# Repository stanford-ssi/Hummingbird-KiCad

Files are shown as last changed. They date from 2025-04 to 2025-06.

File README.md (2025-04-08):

# Hummingbird-KiCad

## Latest Updates

Apr 7, 2025 (Koichi K.): Created the PCB layout. Next steps: figure out power and traces.

Apr 6, 2025 (Sam C.): modified the schematic to be ready for layout. Linked all of the necessary footprints for parts. Added mfr, supplier, cost info. Action item: verification and layout.

Feb 23, 2025 (Victor H., Sam C., Jesse F., Luis S. and Pete!): Modified the KiCad schematic to include correct numbers of PTs, TTs, LCs, etc. (based on P&ID V4). Schematics are organized hierarchically. Problem: Still need to check for input/output conflicts. Action item: can add custom connector footprints next time.

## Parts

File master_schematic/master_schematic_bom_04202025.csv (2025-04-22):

Reference | Value | Datasheet | Footprint | Qty | Manufacturer | Manufacturer Part # | Supplier | Supplier Part # | Unit Cost | Cost @ Qty | Manufacturer 2 | Manufacturer Part # 2 | Supplier 2 | Supplier Part # 2 | Unit Cost 2 | Cost @ Qty 2
U1 | RFM95 | https://learn.adafruit.com/adafruit-rfm69hcw-and-rfm96-rfm95-rfm98-lora-packet-padio-breakouts/overview | hb_footprint_lib:rfm95_connector | 1 | Sullins Connector Solutions | PPPC091LFBN-RC | Digikey | PPPC091LFBN-RC | 0.63 | 0.63 | Sullins Connector Solutions | PPPC051LFBN-RC | Digikey | PPPC051LFBN-RC | 0.43 | 0.43
U9,U10,U11 | HX711 | https://learn.adafruit.com/adafruit-hx711-24-bit-adc | hb_footprint_lib:hx711_connector | 3 | Sullins Connector Solutions | PPPC061LFBN-RC | Digikey | PPPC061LFBN-RC | 0.47 | 0.47
U4,U5,U6,U7,U8 | MCP9600_Module | https://learn.adafruit.com/adafruit-mcp9600-i2c-thermocouple-amplifier/overview | hb_footprint_lib:mcp9600_connector | 5 | Sullins Connector Solutions | PPPC091LFBN-RC | Digikey | PPPC091LFBN-RC | 0.63 | 0.63
SW1 | SW_SPST | Datasheet | hb_footprint_lib:SW_1201M2S3AQE2 | 1 | C&K | 1201M2S3AQE2 | Digikey | CKN5054-ND | 14.68000 | 14.68000
R2,R3,R6,R8,R10,R12,R14,R15,R17 | 2.7K | https://industrial.panasonic.com/cdbs/www-data/pdf/RDM0000/AOA0000C307.pdf | Resistor_SMD:R_0805_2012Metric_Pad1.20x1.40mm_HandSolder | 9 | Panasonic Electronic Components | ERJ-6GEYJ272V | Digikey | P2.7KACT-ND | 0.10 | 0.042
R1,R4,R5,R7,R9,R11,R13,R16,R18 | 1K | https://industrial.panasonic.com/cdbs/www-data/pdf/RDM0000/AOA0000C307.pdf | Resistor_SMD:R_0805_2012Metric_Pad1.20x1.40mm_HandSolder | 9 | Panasonic Electronic Components | ERA-6AEB102V | Digikey | P1.0KDACT-ND | 0.10 | 0.066
Q1,Q2,Q3,Q4,Q5,Q6,Q7,Q8,Q9,Q10 | CWDM3011N TR13 PBFREE | https://my.centralsemi.com/datasheets/CWDM3011N.PDF | Package_SO:SOIC-8_3.9x4.9mm_P1.27mm | 10 | Central Semiconductor Corp | CWDM3011N TR13 PBFREE | Digikey | 1514-CWDM3011NTR13PBFREECT-ND | 1.09 | 1.09
J64,J65,J66,J67,J68,J69,J70,J71,J72,J73,J74,J75,J76,J77,J78,J79,J80,J81,J82,J83 | 1722563102 | https://www.literature.molex.com/SQLImages/kelmscott/Molex/PDF_Images/987651-1008.PDF |  | 20 | Molex | 1722563102 | Digikey | WM26332-ND | 0.30 | 0.25
J34,J35,J36,J37,J38,J39,J40,J41,J42,J43,J44,J45,J46,J47,J48,J49,J50,J51,J52,J53 | 0430250400 | https://tools.molex.com/pdm_docs/ps/PS-43045.pdf |  | 20 | Molex | 0430250400 | Digikey | WM1784-ND | 0.39 | 0.334
J23 | 12V Male | https://www.tme.com/Document/580f3494beb0741fbf705c7febbc9402/XT60H-F.pdf |  | 1 | Changzhou Amass Elec | XT60-F | LCSC | C98734 | 0.3547 | 0.3547
J22 | 5V Male | https://www.mouser.com/datasheet/2/564/JST_B4B_PH_SM4_TB_LF_SN_ePH-3481264.pdf |  | 1 | JST Commercial | PHR-2 | Mouser | 306-PHR-2PP | 0.10 | 0.10
J21 | 5V Female | https://www.mouser.com/datasheet/2/564/JST_B4B_PH_SM4_TB_LF_SN_ePH-3481264.pdf | hb_footprint_lib:JST_S2B-PH-SM4-TB | 1 | JST Commercial | S2B-PH-SM4-TB(LF)(SN) | Mouser | 306-S2BPHSM4TBLFSN | 0.51 | 0.51
J11,J12,J13,J14,J15,J16,J17,J18,J19,J20,J54,J55,J56,J57,J58,J59,J60,J61,J62,J63 | 1723103102 | https://www.molex.com/en-us/products/part-detail/1723103102?display=pdf | hb_footprint_lib:CONN02_1723103102_MOL | 20 | Molex | 1723103102 | Digikey | 900-1723103102-ND | 0.85 | 0.725
J2,J3,J4,J5,J6,J7,J8,J9,J10,J24,J25,J26,J27,J28,J29,J30,J31,J32,J33 | 0430450400 | https://tools.molex.com/pdm_docs/ps/PS-43045.pdf | -- ミックスされた値 -- | 19 | Molex | 0430450400 | Digikey | WM1814-ND | 1.42 | 1.207
J1 | 12V Female | https://www.lcsc.com/datasheet/lcsc_datasheet_2401181031_Changzhou-Amass-Elec-XT60PW-M_C98732.pdf | hb_footprint_lib:AMASS_XT60PW-M | 1 | Changzhou Amass Elec | XT60PW-M | LCSC | C98732 | 0.59 | 0.59
D1,D2,D3,D4,D5,D6,D7,D8,D9,D10 | SBRT20U60SP5-7 | https://www.diodes.com/assets/Datasheets/SBRT20U60SP5.pdf | hb_footprint_lib:POWERDI5_DIO | 10 | Diodes Incorporated | SBRT20U60SP5-7 | Digikey | SBRT20U60SP5-7DICT-ND | 0.78 | 0.78
C1,C2,C3,C4,C5,C6,C7,C8,C9,C10 | 0.1u | https://datasheets.kyocera-avx.com/KGM_X7R.pdf | Capacitor_SMD:C_0805_2012Metric | 10 | KYOCERA AVX | KGM21NR71H104KT | Digikey | 478-KGM21NR71H104KTCT-ND | 0.08 | 0.026

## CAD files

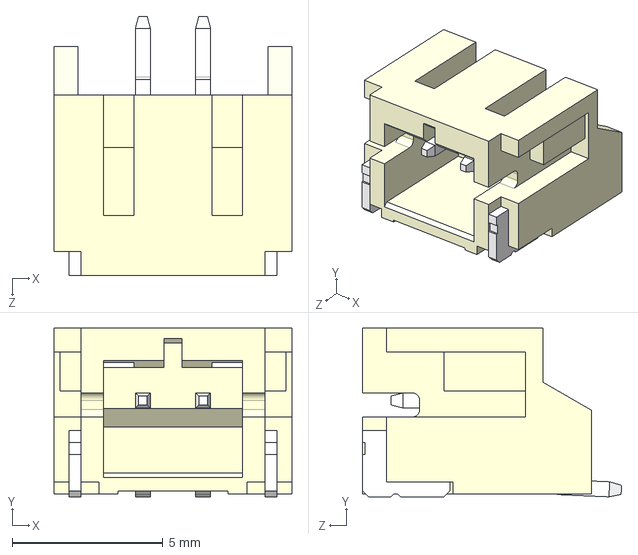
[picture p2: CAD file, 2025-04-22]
3dmodels/S2B-PH-SM4-TB.STEP
7.90 x 5.60 x 8.60 mm

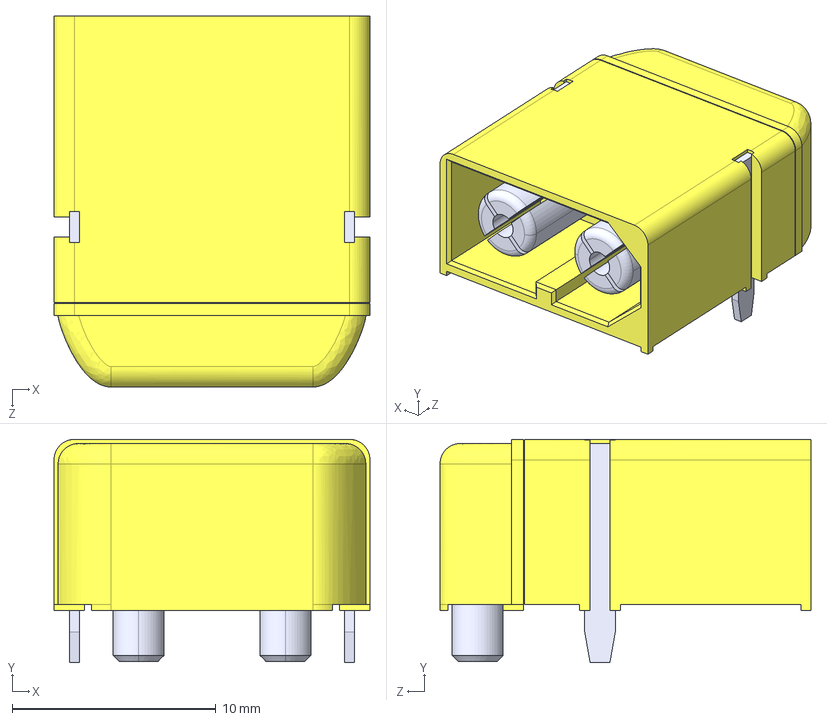
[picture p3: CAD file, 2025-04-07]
3dmodels/XT60PW-M.step
15.5 x 11.0 x 18.2 mm

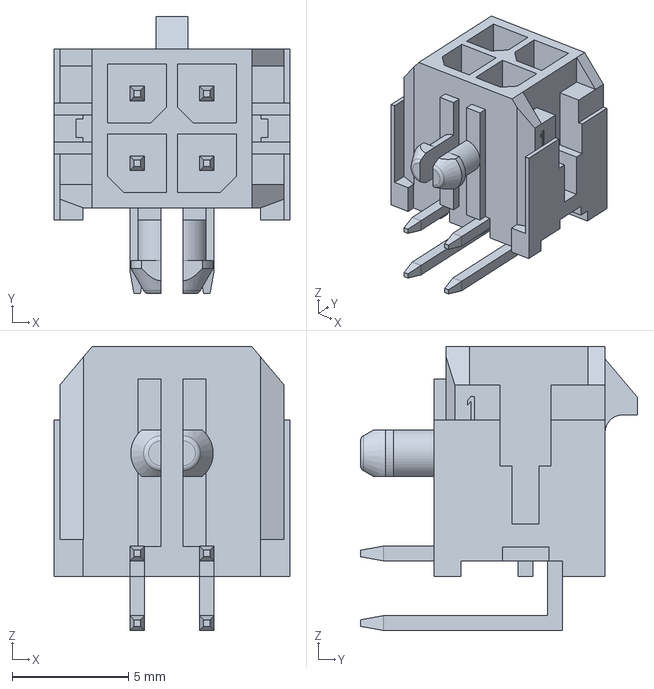
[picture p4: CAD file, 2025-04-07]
3dmodels/430450400.stp
10.2 x 11.9 x 12.2 mm

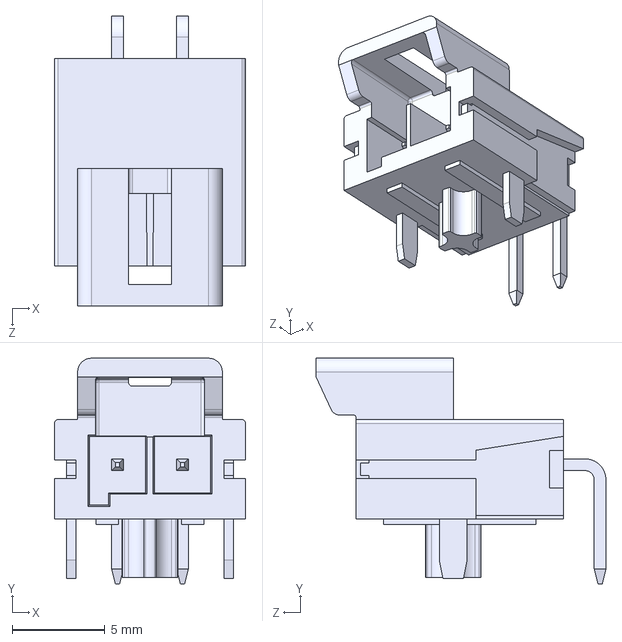
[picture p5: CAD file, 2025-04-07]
3dmodels/1723103102.step
10.3 x 12.2 x 15.6 mm

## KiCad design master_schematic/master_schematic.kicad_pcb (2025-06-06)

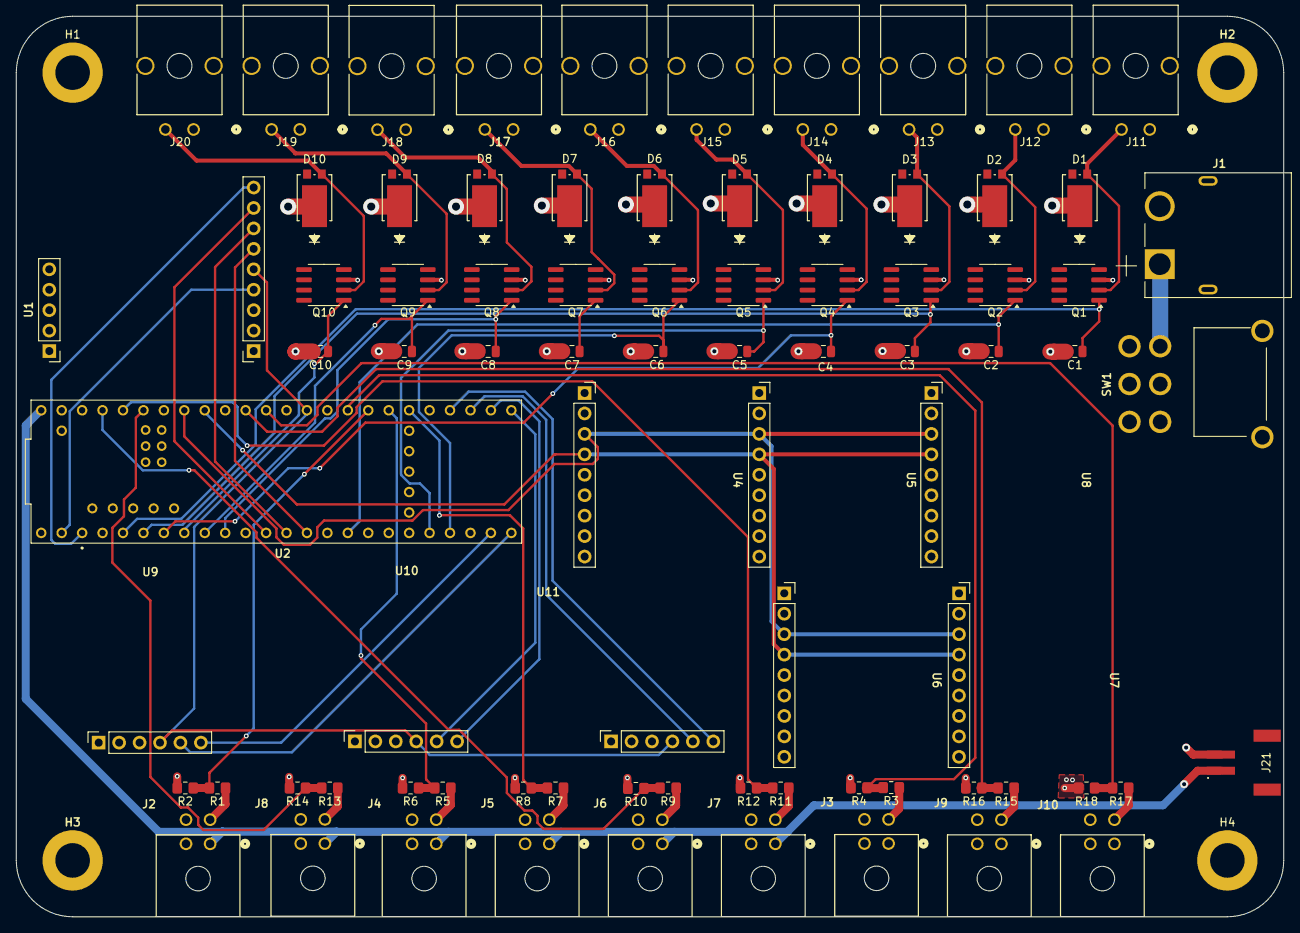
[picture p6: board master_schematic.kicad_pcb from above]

Board: 4 copper layers, 157.5 x 111.9 mm, 85 parts (0 on the bottom side), 57 nets.

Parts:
C1, C2, C3, C4, C5, C6, C7, C8, C9, C10: 0.1u; C_0805_2012Metric
D1, D2, D3, D4, D5, D6, D7, D8, D9, D10: SBRT20U60SP5-7; POWERDI5_DIO
H1, H2, H3, H4: MountingHole; MountingHole_4.3mm_M4_DIN965_Pad
J1: 12V Female; AMASS_XT60PW-M
J2, J3, J4, J5, J6, J7, J8, J9, J10: 0430450400; CONN_SD-43045-001_04_MOL
J11, J12, J13, J14, J15, J16, J17, J18, J19, J20: 1723103102; CONN02_1723103102_MOL
J21: 5V Female; JST_S2B-PH-SM4-TB
Q1, Q2, Q3, Q4, Q5, Q6, Q7, Q8, Q9, Q10: CWDM3011N TR13 PBFREE; SOIC-8_3.9x4.9mm_P1.27mm
R1, R3, R5, R7, R9, R11, R13, R15, R17: 1K; R_0805_2012Metric_Pad1.20x1.40mm_HandSolder
R2, R4, R6, R8, R10, R12, R14, R16, R18: 2.7K; R_0805_2012Metric_Pad1.20x1.40mm_HandSolder
SW1: SW_SPST; SW_1201M2S3AQE2
SYM1: Logo_Open_Hardware_Large; ssilogo
U1: RFM95; rfm95_connector
U2: teensy_4.1; teensy4.1
U4, U5, U6, U7, U8: MCP9600_Module; mcp9600_connector
U9, U10, U11: HX711; hx711_connector

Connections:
+3V3: U1.1 (VDD), U2.3.3V_1 (3.3V), U2.3.3V_2 (3.3V), U2.3.3V_3 (3.3V), U4.1 (VIN), U5.1 (VIN), U6.1 (VIN), U7.1 (VIN), U8.1 (VIN), U9.1 (VIN), U10.1 (VIN), U11.1 (VIN)
+5V: J2.1 (VDD), J4.1 (VDD), J5.1 (VDD), J6.1 (VDD), J7.1 (VDD), J8.1 (VDD), J21.1, U2.VIN
+12V: D1.1 (K), D2.1 (K), D3.1 (K), D4.1 (K), D5.1 (K), D6.1 (K), D7.1 (K), D8.1 (K), D9.1 (K), D10.1 (K), J3.1 (VDD), J9.1 (VDD), J10.1 (VDD), J11.1, J12.1, J13.1, J14.1, J15.1, J16.1, J17.1, J18.1, J19.1, J20.1, SW1.2 (B)
/BV1-O: C10.1, Q10.1 (G), U2.6 (OUT1D)
/BV1-P: C8.1, Q8.1 (G), U2.8 (TX2)
/BV1-T: C9.1, Q9.1 (G), U2.7 (RX2)
/CS_Radio: U1.8 (CS), U2.10 (CS1)
/IRQ: U1.4 (G0), U2.0 (RX1)
/LC1_DATA: U2.32 (OUT1B), U9.5 (DATA)
/LC1_RATE: U2.31 (CTX3), U9.6 (RATE)
/LC2_DATA: U2.33 (MCLK2), U10.5 (DATA)
/LC2_RATE: U2.34 (RX8), U10.6 (RATE)
/LC3_DATA: U2.35 (TX8), U11.5 (DATA)
/LC3_RATE: U2.36 (CS2), U11.6 (RATE)
/MBV1-I-1: C5.1, Q5.1 (G), U2.28 (RX7)
/MBV1-I-2: C6.1, Q6.1 (G), U2.29 (TX7)
/MISO: U1.6 (MISO), U2.12 (MISO)
/MOSI: U1.7 (MOSI), U2.11 (MOSI)
/PT1_I: R9.2, R10.1, U2.23 (A9)
/PT1_N: R3.2, R4.1, U2.41 (A17)
/PT1_O: R1.2, R2.1, U2.40 (A16)
/PT1_P: R5.2, R6.1, U2.39 (A15)
/PT1_T: R7.2, R8.1, U2.38 (A14)
/PT2_I: R11.2, R12.1, U2.22 (A8)
/PT3_I: R13.2, R14.1, U2.21 (A7)
/PT4_I: R15.2, R16.1, U2.16 (A2)
/PT5_I: R17.2, R18.1, U2.15 (A1)
/PV1_N: C1.1, Q1.1 (G), U2.3 (LRCLK2)
/PV1_O: C2.1, Q2.1 (G), U2.24 (A10)
/PV1_P: C3.1, Q3.1 (G), U2.4 (BCLK2)
/PV1_T: C4.1, Q4.1 (G), U2.5 (IN2)
/PV2_O: C7.1, Q7.1 (G)
/RST: U1.9 (RST), U2.1 (TX1)
/SCK: U1.5 (SCK), U2.13 (SCK), U9.4 (SCK), U10.4 (SCK), U11.4 (SCK)
/SCL: U2.19 (A5), U4.3 (SCL), U5.3 (SCL), U6.3 (SCL), U7.3 (SCL), U8.3 (SCL)
/SDA: U2.18 (A4), U4.4 (SDA), U5.4 (SDA), U6.4 (SDA), U7.4 (SDA), U8.4 (SDA)
/pressure_transducers/PT1_I_RAW: J6.3 (DATA), R9.1
/pressure_transducers/PT1_N_RAW: J3.3 (DATA), R3.1
/pressure_transducers/PT1_O_RAW: J2.3 (DATA), R1.1
/pressure_transducers/PT1_P_RAW: J4.3 (DATA), R5.1
/pressure_transducers/PT1_T_RAW: J5.3 (DATA), R7.1
/pressure_transducers/PT2_I_RAW: J7.3 (DATA), R11.1
/pressure_transducers/PT3_I_RAW: J8.3 (DATA), R13.1
/pressure_transducers/PT4_I_RAW: J9.3 (DATA), R15.1
/pressure_transducers/PT5_I_RAW: J10.3 (DATA), R17.1
GND: C1.2, C2.2, C3.2, C4.2, C5.2, C6.2, C7.2, C8.2, C9.2, C10.2, J1.2, J2.2 (GND), J3.2 (GND), J4.2 (GND), J5.2 (GND), J6.2 (GND), J7.2 (GND), J8.2 (GND), J9.2 (GND), J10.2 (GND), J21.2, Q1.3 (S), Q2.3 (S), Q3.3 (S), Q4.3 (S), Q5.3 (S), Q6.3 (S), Q7.3 (S), Q8.3 (S), Q9.3 (S), Q10.3 (S), R2.2, R4.2, R6.2, R8.2, R10.2, R12.2, R14.2, R16.2, R18.2, U1.2 (GND), U2.GND1 (GND), U2.GND2 (GND), U2.GND3 (GND), U2.GND4 (GND), U2.GND5 (GND), U2.USB_GND1 (USB_GND), U2.USB_GND2 (USB_GND), U4.2 (GND), U5.2 (GND), U6.2 (GND), U7.2 (GND), U8.2 (GND), U9.3 (GND), U10.3 (GND), U11.3 (GND)
unnamed: D1.2 (A), J11.2, Q1.2 (D)
unnamed: D2.2 (A), J12.2, Q2.2 (D)
unnamed: D3.2 (A), J13.2, Q3.2 (D)
unnamed: D4.2 (A), J14.2, Q4.2 (D)
unnamed: D5.2 (A), J15.2, Q5.2 (D)
unnamed: D6.2 (A), J16.2, Q6.2 (D)
unnamed: D7.2 (A), J17.2, Q7.2 (D)
unnamed: D8.2 (A), J18.2, Q8.2 (D)
unnamed: D9.2 (A), J19.2, Q9.2 (D)
unnamed: D10.2 (A), J20.2, Q10.2 (D)
unnamed: J1.1, SW1.1 (A)

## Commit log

2024-12-04 Add files via upload
    Added KiCAD files from previous hummingbird repo
2025-01-20 master_schematic update
    [master_schematic.kicad_pcb, master_schematic.kicad_sch]
2025-01-25 added footprint library and a pcb file
    [master_schematic.kicad_pcb, master_schematic.kicad_sch]
2025-02-22 Added symbol libraries for HX711 and the transistor IRLZ34NPBF. Made schematic for solenoid valve.
    [master_schematic.kicad_sch]
2025-02-23 added sheet and connections for PT
    [master_schematic.kicad_sch, pts.kicad_sch]
2025-02-23 PT update
    [master_schematic.kicad_sch, pts.kicad_sch]
2025-02-24 full master schematic in hierarchical format
    [lcs.kicad_sch, master_schematic.kicad_sch, pvs.kicad_sch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]
2025-02-24 minor updates
    [lcs.kicad_sch, master_schematic.kicad_sch]
2025-04-07 modified for PCB development
    [1723103102.step, master_schematic.kicad_sch, pts.kicad_sch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]
2025-04-07 updated with part info
    [430450400.stp, XT60PW-M.step, lcs.kicad_sch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]
2025-04-08 fixed errors on schematic
    [lcs.kicad_sch, master_schematic.kicad_pcb, master_schematic.kicad_sch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]
2025-04-08 patch fix
    [lcs.kicad_sch]
2025-04-08 finished building PCB
    [lcs.kicad_sch, master_schematic.kicad_pcb, master_schematic.kicad_sch]
2025-04-11 updated BOM
    [lcs.kicad_sch, master_schematic.csv, master_schematic.kicad_pcb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]
2025-04-14 pcb layout and traces made (partially)
    [master_schematic.kicad_pcb]
2025-04-15 updated BOM materials
2025-04-15 added decoupling capacitors, fixed voltage values for TTs and load cells to +3V3
    [lcs.kicad_sch, master_schematic.csv, pts.kicad_sch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]
2025-04-20 finding parts
    [master_schematic.kicad_sch, master_schematic_bom_04202025.csv, pts.kicad_sch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]
2025-04-22 edits after bom
    [master_schematic.kicad_sch, master_schematic_bom_04202025.csv, pts.kicad_sch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]
2025-04-22 updated schematic for PT
    [pts.kicad_sch]
2025-04-22 adding library items
    [S2B-PH-SM4-TB.STEP]
2025-04-22 fixed errors, redesigned PCB layout
    [master_schematic.kicad_pcb]
2025-04-22 redid power layer
    [master_schematic.kicad_pcb]
2025-05-06 routed some annoying ass traces
    [master_schematic.kicad_pcb, master_schematic.kicad_sch, pts.kicad_sch]
2025-05-13 FINALLY FINISHED ThESE DAMN TRACES F&#%%%
    [master_schematic.kicad_sch]
2025-06-06 I dont know what change this is lol
    [master_schematic.kicad_pcb]
2025-06-06 Edited the switch to be in series with the circuit (instead of parallel)
    [master_schematic.kicad_pcb, master_schematic.kicad_sch]
2025-06-06 Edited silkscreens
    [master_schematic.kicad_pcb, master_schematic.kicad_sch]
